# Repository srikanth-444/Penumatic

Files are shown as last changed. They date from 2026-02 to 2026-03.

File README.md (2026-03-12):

# _Peumatic Backpack_
This is a Penumatic System that senses and actuates the multiple soft actuators while communicating with the remote pc 

## _Hardware_ 
To control and sense the robotic actuator system, developed using KiCad 8, this repository will build the Gerber files of the system upon pushing the action artifacts specific to JLCPCB 

| Component | Function | Notes |
| --- | --- | --- |
| **ESP-32 S3** | Microcontroller | Handles system control, communication, and overall logic |
| **LTC2498** | 24-bit ADC | Senses actuator position with high precision |
| **LTC6906** | External oscillator | Provides clock signal for ADC operation |
| **MCZ33996**  | Solenoid driver | Actuates solenoidal valves based on control signals |

## _Firmware_ 
Developed in C using FreeRTOS for increased concurrency. Code is developed using VSCode ESP-IDF extension

### Images
<p align="center">
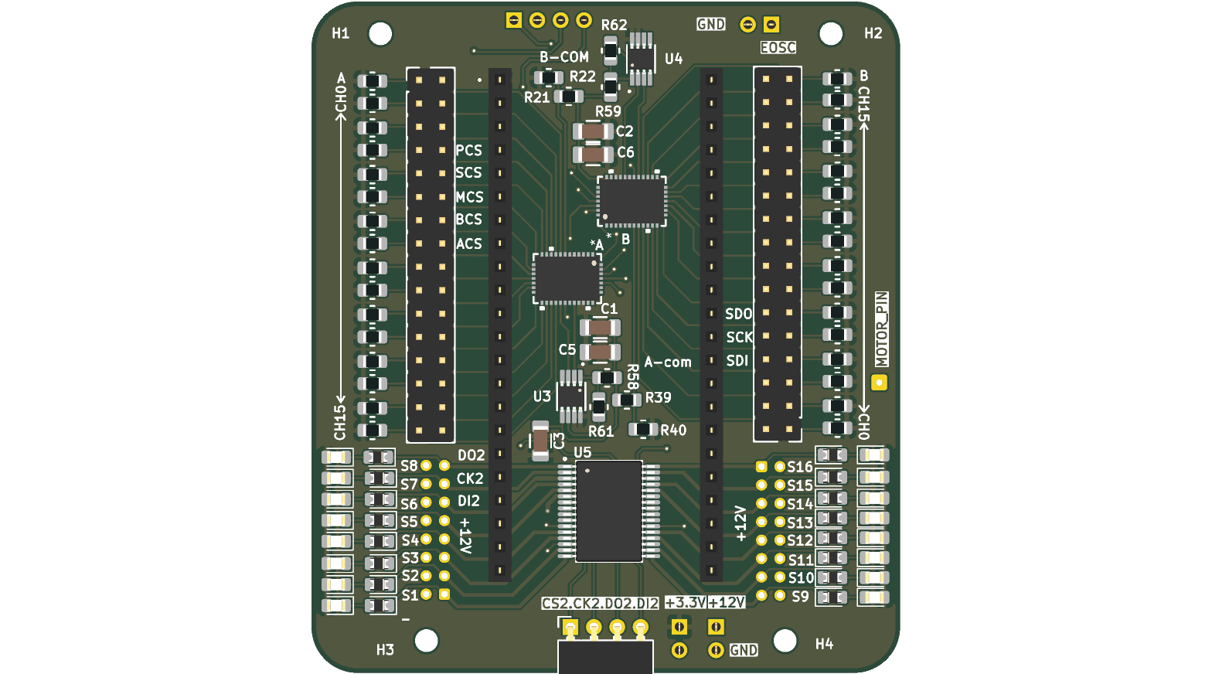
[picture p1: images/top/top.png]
  
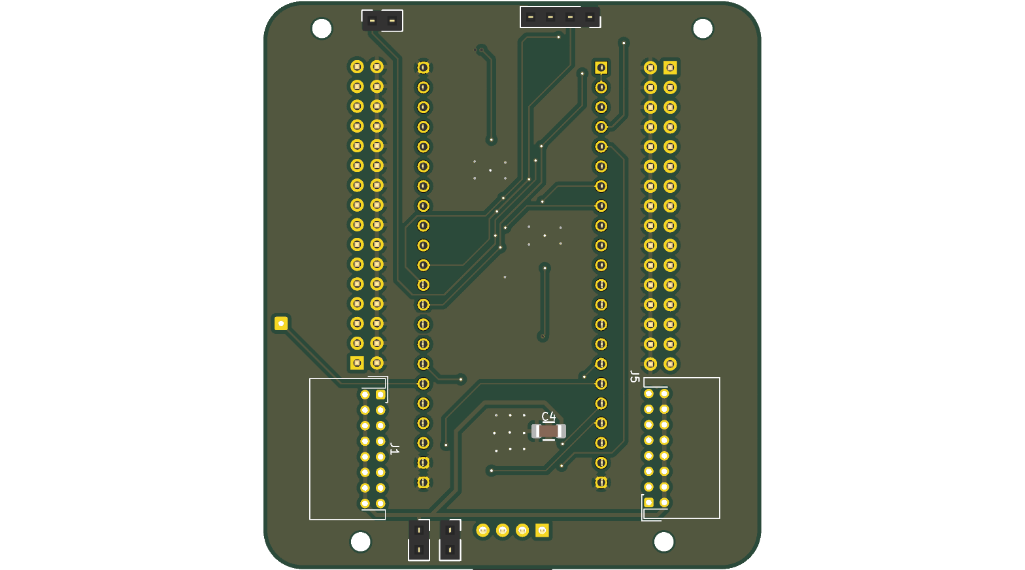
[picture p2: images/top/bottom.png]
  
</p>
<p align="center">
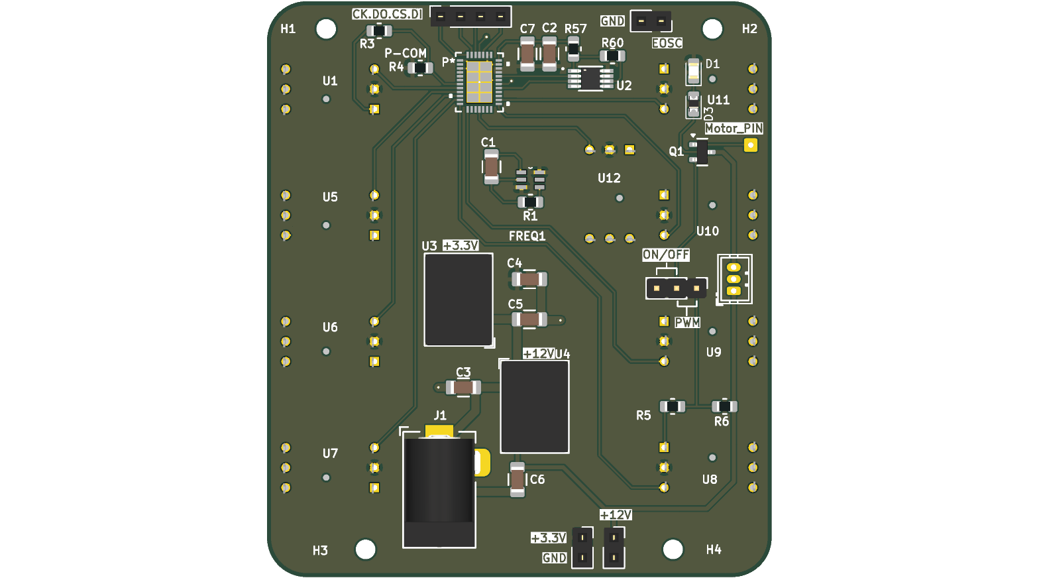
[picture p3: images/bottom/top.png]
  
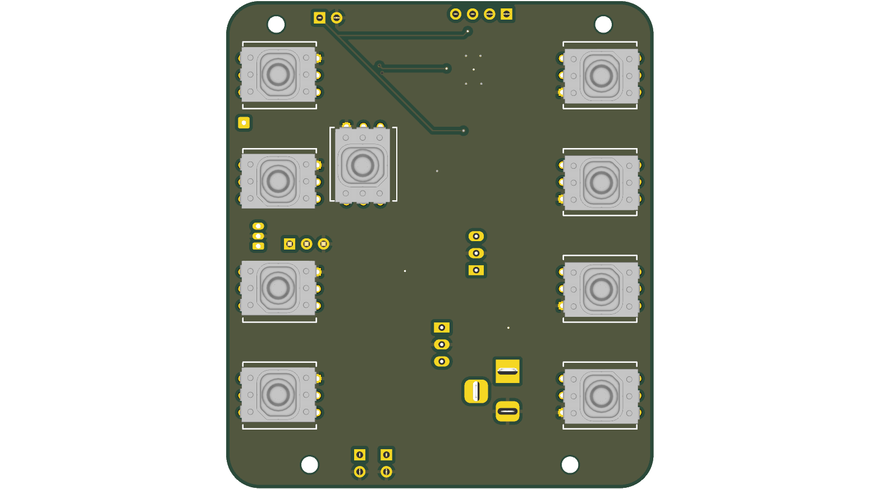
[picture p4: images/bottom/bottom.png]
  
</p>
rendered with [kicad-render](https://github.com/linalinn/kicad-render)

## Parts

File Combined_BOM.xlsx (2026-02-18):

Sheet: pneumatic Backpack v3.0_BOM
Reference | Value | Datasheet | Footprint | Qty | DNP
A1 | LTC2498IUHF_TRPBF |  | mod:QFN-38_UHF | 1
Bus_D1 | Conn_01x04_Pin | ~ | Connector_PinSocket_2.54mm:PinSocket_1x04_P2.54mm_Vertical | 1
C1 | 5pf | ~ | Capacitor_SMD:C_1206_3216Metric_Pad1.33x1.80mm_HandSolder | 1
C2 | 0.1uf | ~ | Capacitor_SMD:C_1206_3216Metric_Pad1.33x1.80mm_HandSolder | 1
C3,C4,C5,C6 | 4.7uf | ~ | Capacitor_SMD:C_1206_3216Metric_Pad1.33x1.80mm_HandSolder | 4
C7 | 10uf | ~ | Capacitor_SMD:C_1206_3216Metric_Pad1.33x1.80mm_HandSolder | 1
D1 | LED | ~ | LED_SMD:LED_0805_2012Metric_Pad1.15x1.40mm_HandSolder | 1
D3 | D | ~ | Diode_SMD:D_0805_2012Metric_Pad1.15x1.40mm_HandSolder | 1
FREQ1 | LTC6906IS6_TRPBF |  | mod:SOT95P280X100-6N | 1
J1 | Barrel_Jack_MountingPin | ~ | Connector_BarrelJack:BarrelJack_Horizontal | 1
J2,J9,J11 | Conn_01x02_Pin | ~ | Connector_PinSocket_2.54mm:PinSocket_1x02_P2.54mm_Vertical | 3
J3,J4 | Conn_01x03_Pin | ~ | -- mixed values -- | 2
J5 | Conn_01x01_Pin | ~ | Connector_Wire:SolderWire-0.15sqmm_1x01_D0.5mm_OD1.5mm | 1
Q1 | AO3400A | http://www.aosmd.com/pdfs/datasheet/AO3400A.pdf | Package_TO_SOT_SMD:SOT-23 | 1
R1,R3,R4,R57,R60 | 100k | ~ | Resistor_SMD:R_0805_2012Metric_Pad1.20x1.40mm_HandSolder | 5
R5 | 70 | ~ | Resistor_SMD:R_0805_2012Metric_Pad1.20x1.40mm_HandSolder | 1
R6 | 50 | ~ | Resistor_SMD:R_0805_2012Metric_Pad1.20x1.40mm_HandSolder | 1
U1,U5,U6,U7,U8,U9,U10,U11,U12 | ABPDLNN100MG2A3 |  | ABPDLNN100MG2A3:XDCR_ABPDLNN100MG2A3 | 9
U2 | INA332AIDGKR |  | INA332AIDGKR:SOP65P490X110-8N | 1
U3 | R-78C3.3-1.0 | https://www.recom-power.com/pdf/Innoline/R-78Cxx-1.0.pdf | Converter_DCDC:Converter_DCDC_RECOM_R-78E-0.5_THT | 1
U4 | R-78C12-1.0 | https://www.recom-power.com/pdf/Innoline/R-78Cxx-1.0.pdf | Converter_DCDC:Converter_DCDC_RECOM_R-78E-0.5_THT | 1

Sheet: pneumatic Backpack v3.1_BOM
Reference | Value | Datasheet | Footprint | Qty | DNP
A2,A3 | LTC2498IUHF_TRPBF |  | mod:QFN-38_UHF | 2
Bus_D1,Bus_D2 | Conn_01x04_Pin | ~ | -- mixed values -- | 2
C1,C2,C3,C4 | 10uf | ~ | Capacitor_SMD:C_1206_3216Metric_Pad1.33x1.80mm_HandSolder | 4
C5,C6 | 0.1uf | ~ | Capacitor_SMD:C_1206_3216Metric_Pad1.33x1.80mm_HandSolder | 2
D1,D2,D3,D4,D5,D6,D7,D8,D9,D10,D11,D12,D13,D14,D15,D16 | LED | ~ | LED_SMD:LED_0805_2012Metric_Pad1.15x1.40mm_HandSolder | 16
J1,J5 | Conn_01x12_Pin | ~ | Connector_JST:JST_ZH_B12B-ZR_1x12_P1.50mm_Vertical | 2
J2 | Conn_01x01_Pin | ~ | Connector_Wire:SolderWire-0.15sqmm_1x01_D0.5mm_OD1.5mm | 1
J3,J4 | Conn_02x16_Top_Bottom | ~ | Connector_PinHeader_2.54mm:PinHeader_2x16_P2.54mm_Vertical | 2
J9,J10,J11 | Conn_01x02_Pin | ~ | Connector_PinSocket_2.54mm:PinSocket_1x02_P2.54mm_Vertical | 3
R21,R22,R23,R24,R25,R26,R27,R28,R29,R30,R31,R32,R33,R34,R35,R36,R37,R38,R39,R40,R41,R42,R43,R44,R45,R46,R47,R48,R49,R50,R51,R52,R53,R54,R55,R56,R58,R59,R61,R62 | 100k | ~ | Resistor_SMD:R_0805_2012Metric_Pad1.20x1.40mm_HandSolder | 40
U1 | ESP32-S3-DEVKITC-1-N8R2 |  | ESP32-S3-DEVKITC-1-N8R2:XCVR_ESP32-S3-DEVKITC-1-N8R2 | 1
U3,U4 | INA332AIDGKR |  | INA332AIDGKR:SOP65P490X110-8N | 2
U5 | MCZ33996EK |  | MCZ33996EK:SOP65P1030X265-33N | 1

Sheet: Summary
Value | Qty
0.1uf | 3
100k | 45
10uf | 5
4.7uf | 4
50 | 1
5pf | 1
70 | 1
ABPDLNN100MG2A3 | 9
AO3400A | 1
Barrel_Jack_MountingPin | 1
Conn_01x01_Pin | 2
Conn_01x02_Pin | 6
Conn_01x03_Pin | 2
Conn_01x04_Pin | 3
Conn_01x12_Pin | 2
Conn_02x16_Top_Bottom | 2
D | 1
ESP32-S3-DEVKITC-1-N8R2 | 1
INA332AIDGKR | 3
LED | 17
LTC2498IUHF_TRPBF | 3
LTC6906IS6_TRPBF | 1
MCZ33996EK | 1
R-78C12-1.0 | 1
R-78C3.3-1.0 | 1

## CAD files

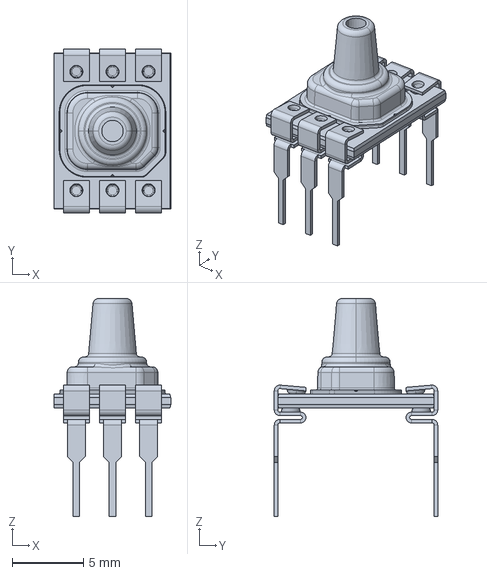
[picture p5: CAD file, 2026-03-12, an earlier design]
Hardware/pneumatic Backpack v3.0/ABPDLNN100MG2A3/ABP2 Series CAD Models/honeywell-abp2-series-32351540_DIP_VN_DRY_a.stp
8.20 x 11.5 x 15.3 mm

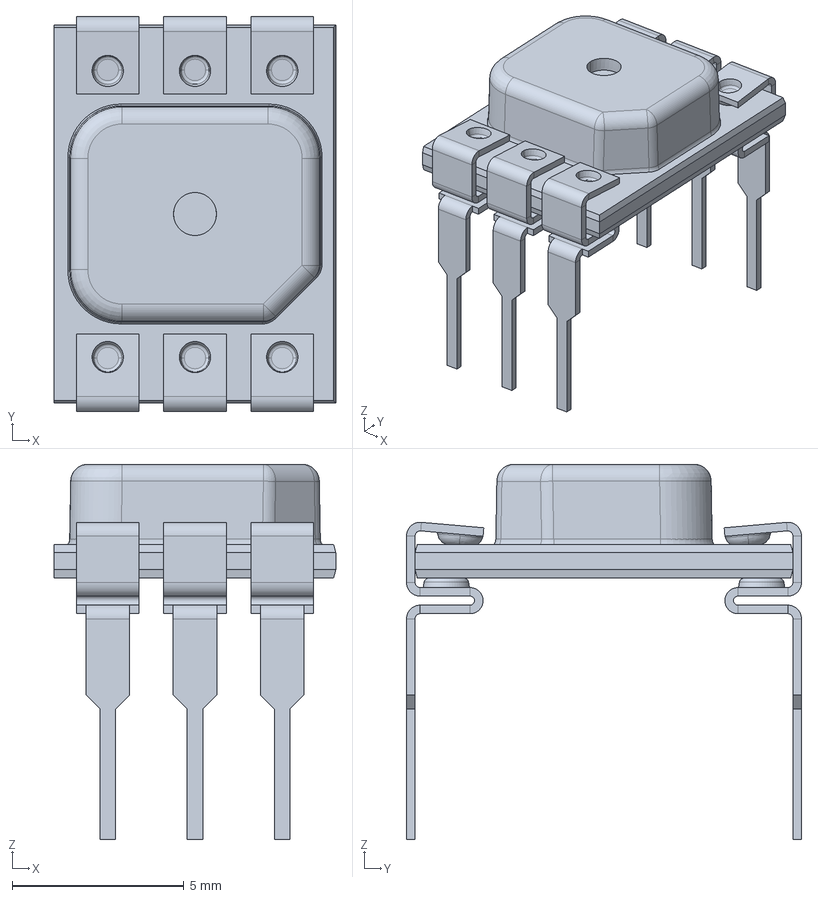
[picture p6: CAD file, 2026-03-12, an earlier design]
Hardware/pneumatic Backpack v3.0/ABPDLNN100MG2A3/honeywell-abp2-series-32351541_DIP_NN_DRY_a.stp
8.20 x 11.5 x 10.9 mm

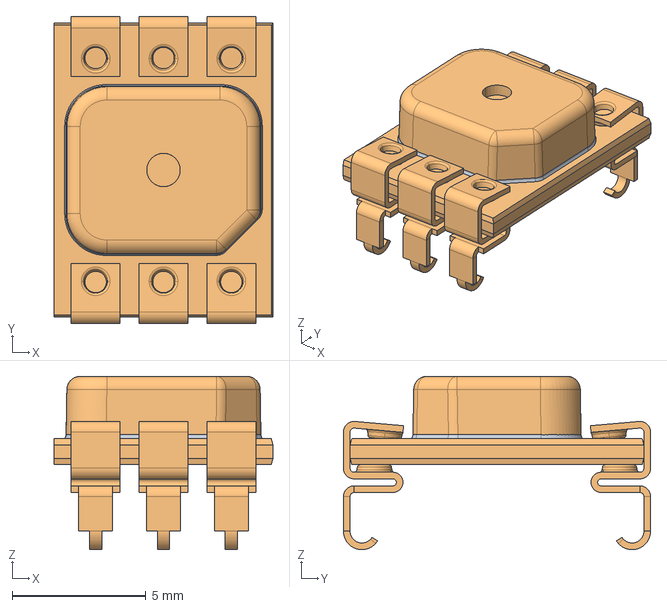
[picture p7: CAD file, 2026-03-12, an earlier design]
Hardware/pneumatic Backpack v3.0/ABPDLNN100MG2A3/ABP2 Series CAD Models/honeywell-abp2-series-32351537_SMT_NN_DRY_a.stp
8.20 x 11.5 x 6.49 mm

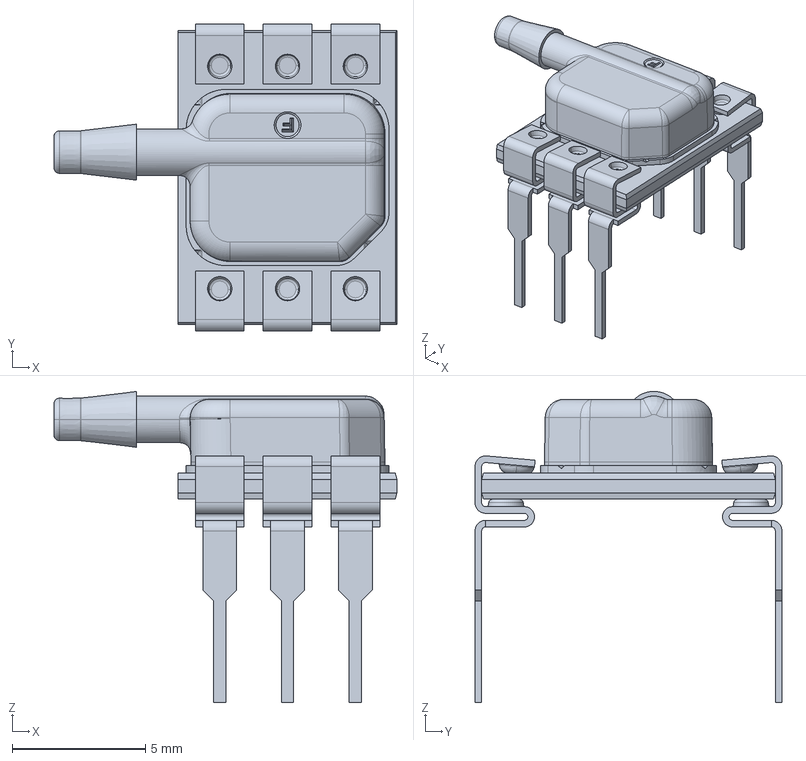
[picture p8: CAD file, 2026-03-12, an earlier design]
Hardware/pneumatic Backpack v3.0/ABPDLNN100MG2A3/honeywell-abp2-series-32351350_DIP_RN_WET_a.stp
12.8 x 11.5 x 11.7 mm

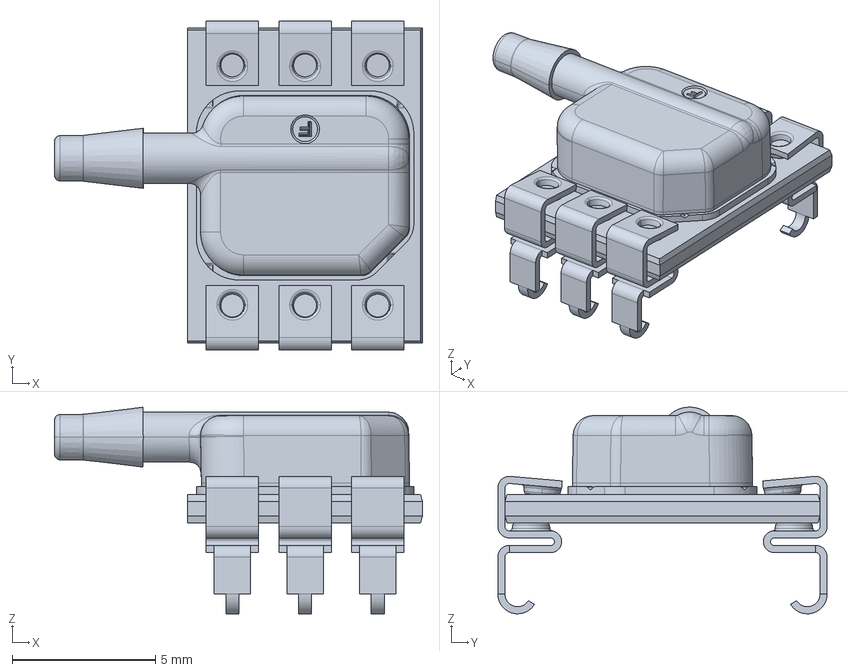
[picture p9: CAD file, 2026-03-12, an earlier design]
Hardware/pneumatic Backpack v3.0/ABPDLNN100MG2A3/ABP2 Series CAD Models/honeywell-abp2-series-32351002_SMT_RN_WET_a.stp
12.8 x 11.5 x 7.22 mm

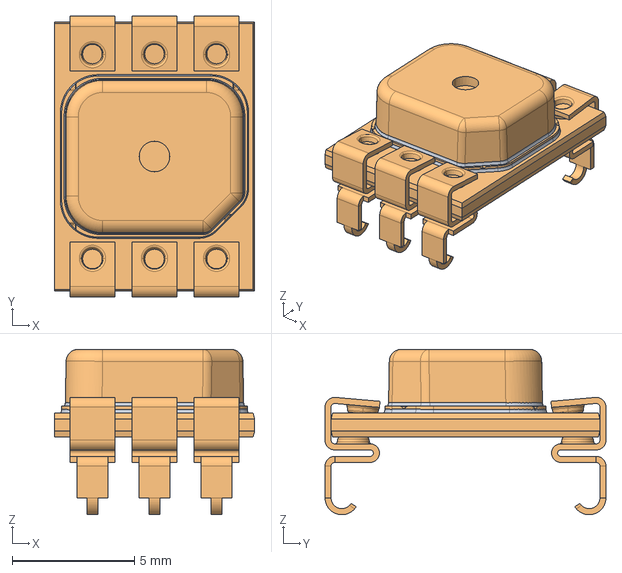
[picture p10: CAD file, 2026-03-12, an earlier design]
Hardware/pneumatic Backpack v3.0/ABPDLNN100MG2A3/ABP2 Series CAD Models/honeywell-abp2-series-32351537_SMT_NN_WET_a.stp
8.20 x 11.5 x 6.77 mm

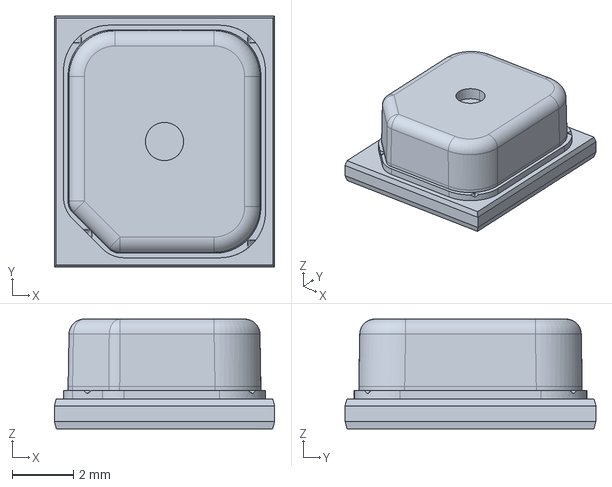
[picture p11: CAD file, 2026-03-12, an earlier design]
Hardware/pneumatic Backpack v3.0/ABPDLNN100MG2A3/ABP2 Series CAD Models/honeywell-abp2-series-32347847_LL_NN_WET_a.stp
7.20 x 8.20 x 3.59 mm

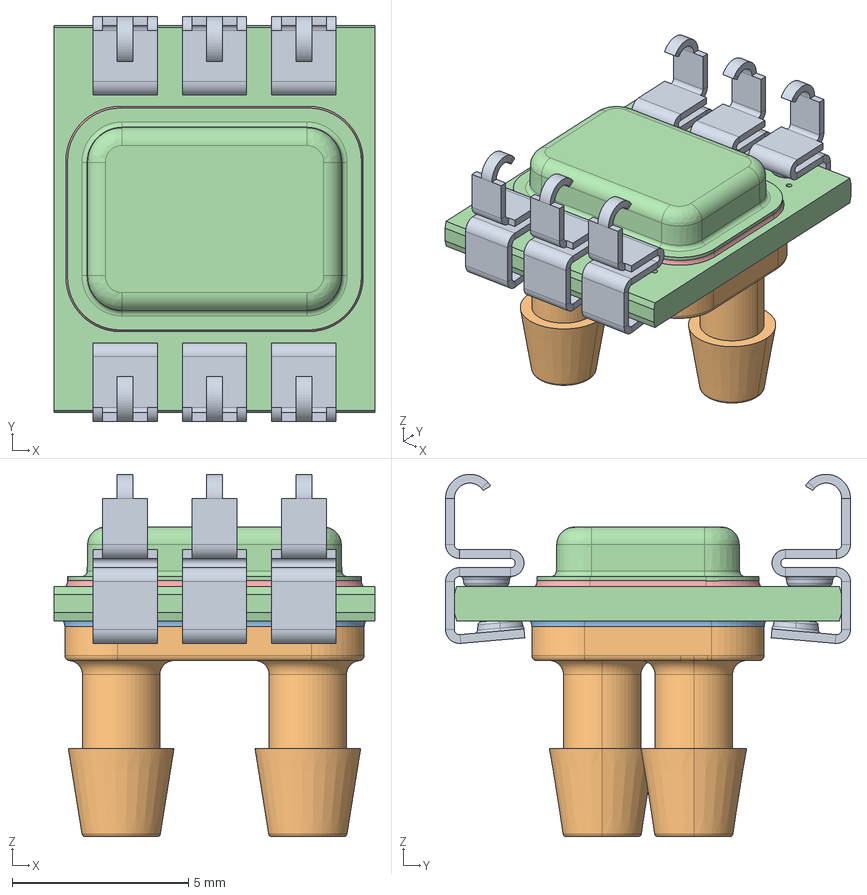
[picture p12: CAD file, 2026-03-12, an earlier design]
Hardware/pneumatic Backpack v3.0/ABPDLNN100MG2A3/ABP2 Series CAD Models/honeywell-abp2-series-32349646_SMT_DA_DRY_a.stp
9.10 x 11.5 x 10.3 mm
MSBR-40_1
MSBR-39_1
MSBR-38_1
MSBR-37_1
MSBR-36_1
MSBR-35_1
MSBR-34_1
MSBR-33_1
MSBR-32_1
MSBR-31_1
MSBR-30_1
MSBR-29_1
MSBR-28_1
MSBR-27_1
MSBR-26_1
MSBR-25_1
MSBR-24_1
MSBR-23_1
MSBR-22_1
MSBR-21_1
MSBR-20_1
MSBR-19_1
MSBR-18_1
MSBR-17_1
MSBR-16_1
MSBR-15_1
MSBR-14_1
MSBR-13_1
MSBR-12_1
MSBR-11_1
MSBR-10_1
MSBR-9_1
MSBR-8_1
MSBR-7_1
MSBR-6_1
MSBR-5_1
MSBR-4_1
MSBR-3_1
MSBR-2_1
MSBR-1_1

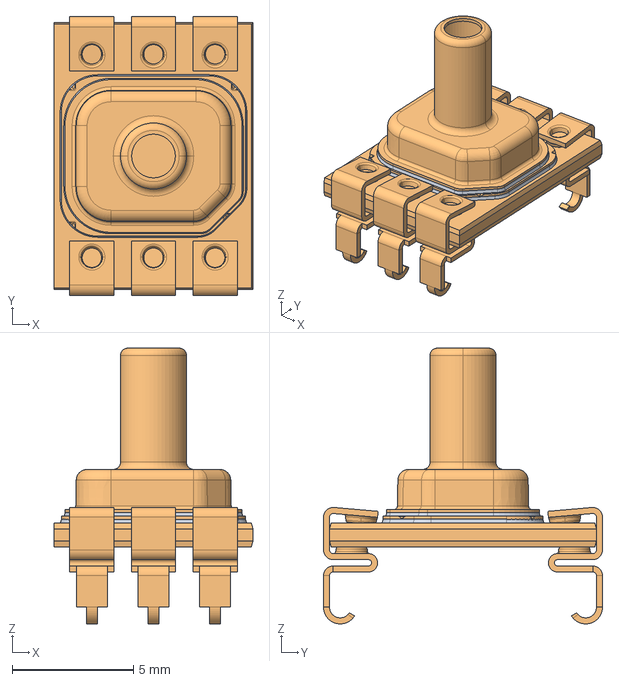
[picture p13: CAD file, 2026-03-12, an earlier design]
Hardware/pneumatic Backpack v3.0/ABPDLNN100MG2A3/ABP2 Series CAD Models/honeywell-abp2-series-32351534_SMT_SN_WET_a.stp
8.20 x 11.5 x 11.4 mm

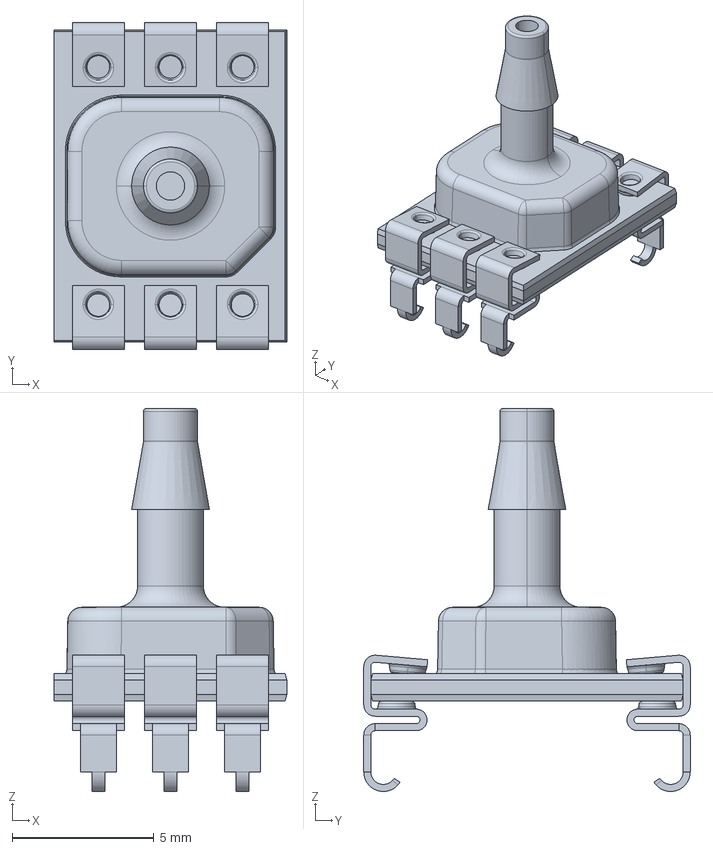
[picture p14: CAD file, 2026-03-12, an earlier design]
Hardware/pneumatic Backpack v3.0/ABPDLNN100MG2A3/ABP2 Series CAD Models/honeywell-abp2-series-32351535_SMT_AN_DRY_a.stp
8.20 x 11.5 x 13.5 mm

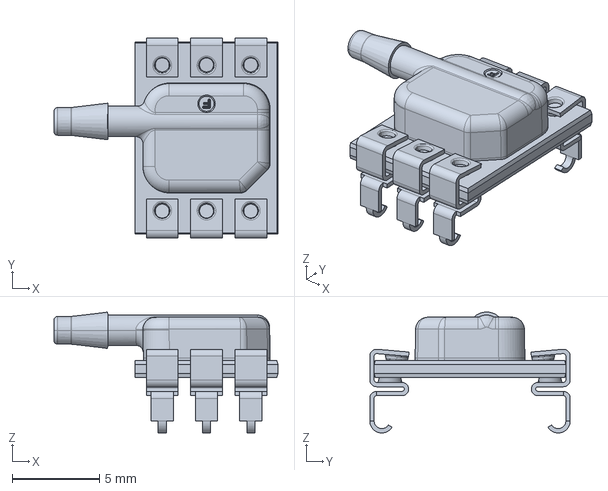
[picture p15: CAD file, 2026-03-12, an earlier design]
Hardware/pneumatic Backpack v3.0/ABPDLNN100MG2A3/ABP2 Series CAD Models/honeywell-abp2-series-32351002_SMT_RN_DRY_a.stp
12.8 x 11.5 x 6.94 mm

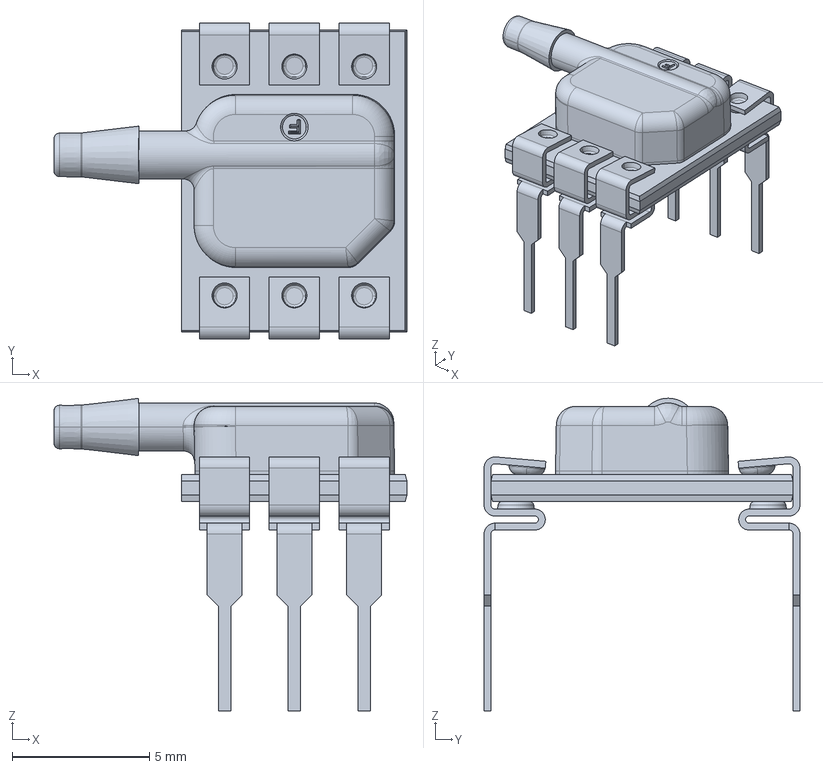
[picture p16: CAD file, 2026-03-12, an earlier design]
Hardware/pneumatic Backpack v3.0/ABPDLNN100MG2A3/ABP2 Series CAD Models/honeywell-abp2-series-32351350_DIP_RN_DRY_a.stp
12.8 x 11.5 x 11.4 mm

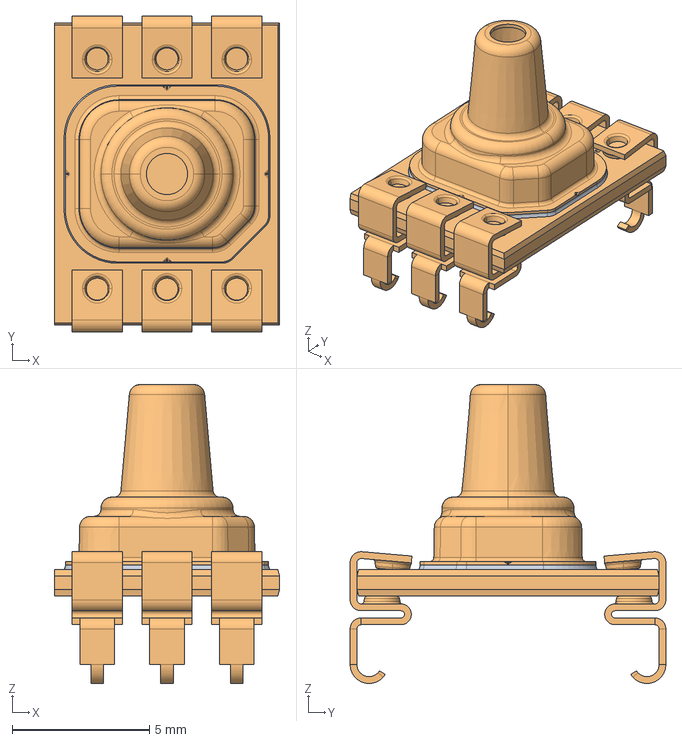
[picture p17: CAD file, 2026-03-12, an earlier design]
Hardware/pneumatic Backpack v3.0/ABPDLNN100MG2A3/ABP2 Series CAD Models/honeywell-abp2-series-32351536_SMT_VN_DRY_a.stp
8.20 x 11.5 x 10.9 mm

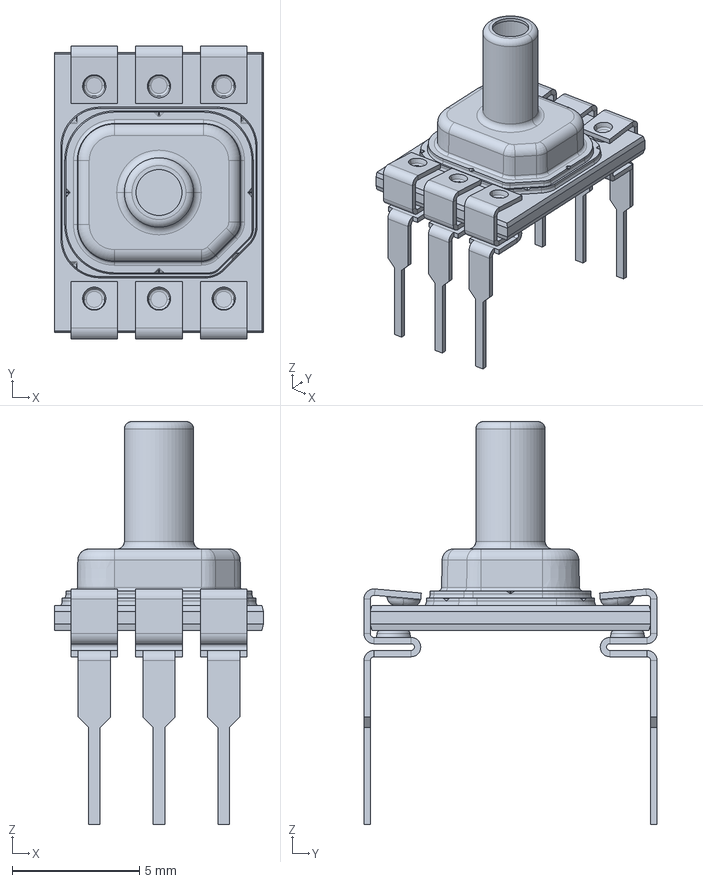
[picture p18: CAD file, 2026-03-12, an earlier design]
Hardware/pneumatic Backpack v3.0/ABPDLNN100MG2A3/ABP2 Series CAD Models/honeywell-abp2-series-32351538_DIP_SN_WET_a.stp
8.20 x 11.5 x 15.8 mm

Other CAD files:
Hardware/pneumatic Backpack v3.0/ABPDLNN100MG2A3/ABP2 Series CAD Models/honeywell-abp2-series-32351536_SMT_VN_WET_a.stp
Hardware/pneumatic Backpack v3.0/ABPDLNN100MG2A3/ABP2 Series CAD Models/honeywell-abp2-series-32349647_DIP_DA_DRY_a.stp
Hardware/pneumatic Backpack v3.0/ABPDLNN100MG2A3/ABP2 Series CAD Models/honeywell-abp2-series-32351535_SMT_AN_WET_a.stp
Hardware/pneumatic Backpack v3.0/ABPDLNN100MG2A3/ABP2 Series CAD Models/honeywell-abp2-series-32351309_DIP_RR_DRY_a.stp
Hardware/pneumatic Backpack v3.0/ABPDLNN100MG2A3/ABP2 Series CAD Models/honeywell-abp2-series-32347845_LL_AN_WET_a.stp
Hardware/pneumatic Backpack v3.0/ABPDLNN100MG2A3/ABP2 Series CAD Models/honeywell-abp2-series-32347846_LL_SN_WET_a.stp
Hardware/pneumatic Backpack v3.0/ABPDLNN100MG2A3/ABP2 Series CAD Models/honeywell-abp2-series-32347847_LL_NN_DRY_a.stp
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

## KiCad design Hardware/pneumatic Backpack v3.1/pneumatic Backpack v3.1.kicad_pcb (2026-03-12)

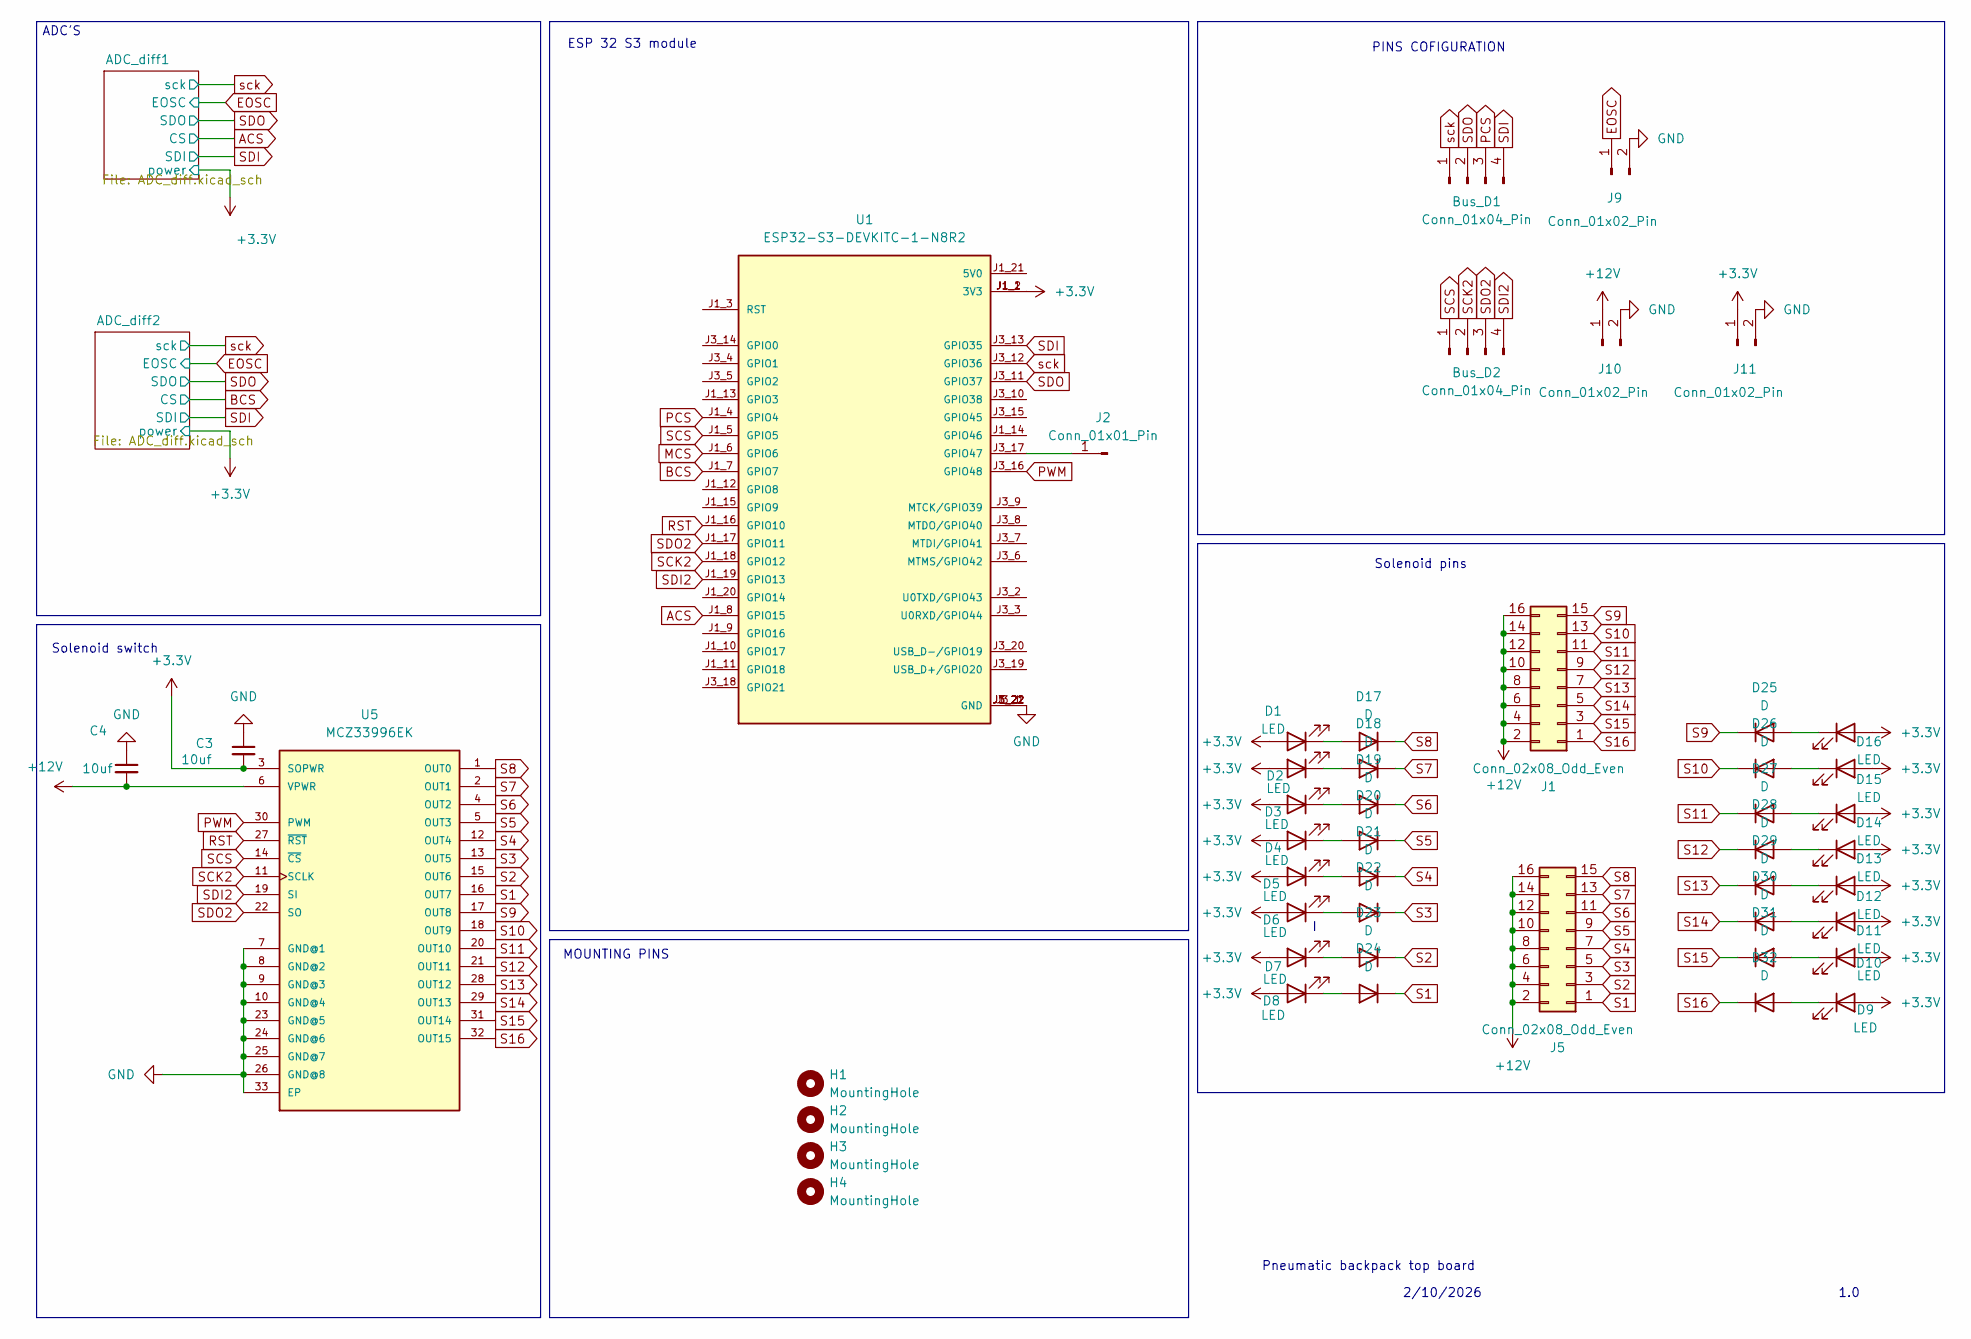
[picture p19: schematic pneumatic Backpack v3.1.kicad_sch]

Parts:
Bus_D1: Conn_01x04_Pin; PinSocket_1x04_P2.54mm_Vertical
Bus_D2: Conn_01x04_Pin; PinSocket_1x04_P2.54mm_Horizontal
C3, C4: 10uf; C_1206_3216Metric_Pad1.33x1.80mm_HandSolder
D1, D2, D3, D4, D5, D6, D7, D8, D9, D10, D11, D12, D13, D14, D15, D16: LED; LED_0805_2012Metric_Pad1.15x1.40mm_HandSolder
D17, D18, D19, D20, D21, D22, D23, D24, D25, D26, D27, D28, D29, D30, D31, D32: D; D_0805_2012Metric_Pad1.15x1.40mm_HandSolder
H1, H2, H3, H4: MountingHole; MountingHole_2.5mm
J1, J5: Conn_02x08_Odd_Even; JST_PHD_S16B-PHDSS_2x08_P2.00mm_Horizontal
J2: Conn_01x01_Pin; SolderWire-0.15sqmm_1x01_D0.5mm_OD1.5mm
J9, J10, J11: Conn_01x02_Pin; PinSocket_1x02_P2.54mm_Vertical
U1: ESP32-S3-DEVKITC-1-N8R2; XCVR_ESP32-S3-DEVKITC-1-N8R2; PARTREV V1
U5: MCZ33996EK; SOP65P1030X265-33N

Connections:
+3.3V: C3.2, D1.2 (A), D2.2 (A), D3.2 (A), D4.2 (A), D5.2 (A), D6.2 (A), D7.2 (A), D8.2 (A), D9.2 (A), D10.2 (A), D11.2 (A), D12.2 (A), D13.2 (A), D14.2 (A), D15.2 (A), D16.2 (A), J11.1, U1.J1_1 (3V3), U1.J1_2 (3V3), U5.3 (SOPWR); also elsewhere on the board
+12V: C4.2, J1.2, J1.4, J1.6, J1.8, J1.10, J1.12, J1.14, J1.16, J5.2, J5.4, J5.6, J5.8, J5.10, J5.12, J5.14, J5.16, J10.1, U5.6 (VPWR)
ACS: U1.J1_8 (GPIO15); also elsewhere on the board
BCS: U1.J1_7 (GPIO7); also elsewhere on the board
EOSC: J9.1; also elsewhere on the board
GND: C3.1, C4.1, J9.2, J10.2, J11.2, U1.J1_22 (GND), U1.J3_1 (GND), U1.J3_21 (GND), U1.J3_22 (GND), U5.7 (GND@1), U5.8 (GND@2), U5.9 (GND@3), U5.10 (GND@4), U5.23 (GND@5), U5.24 (GND@6), U5.25 (GND@7), U5.26 (GND@8), U5.33 (EP); also elsewhere on the board
MCS: U1.J1_6 (GPIO6)
unnamed: D1.1 (K), D17.2 (A)
unnamed: D10.1 (K), D31.2 (A)
unnamed: D11.1 (K), D30.2 (A)
unnamed: D12.1 (K), D29.2 (A)
unnamed: D13.1 (K), D28.2 (A)
unnamed: D14.1 (K), D27.2 (A)
unnamed: D15.1 (K), D26.2 (A)
unnamed: D16.1 (K), D25.2 (A)
unnamed: D2.1 (K), D18.2 (A)
unnamed: D3.1 (K), D19.2 (A)
unnamed: D4.1 (K), D20.2 (A)
unnamed: D5.1 (K), D21.2 (A)
unnamed: D6.1 (K), D22.2 (A)
unnamed: D7.1 (K), D23.2 (A)
unnamed: D8.1 (K), D24.2 (A)
unnamed: D9.1 (K), D32.2 (A)
unnamed: J2.1, U1.J3_17 (GPIO47)
PCS: Bus_D1.3, U1.J1_4 (GPIO4)
PWM: U1.J3_16 (GPIO48), U5.30 (PWM)
RST: U1.J1_16 (GPIO10), U5.27 (~RST)
S1: D24.1 (K), J5.1, U5.16 (OUT7)
S2: D23.1 (K), J5.3, U5.15 (OUT6)
S3: D22.1 (K), J5.5, U5.13 (OUT5)
S4: D21.1 (K), J5.7, U5.12 (OUT4)
S5: D20.1 (K), J5.9, U5.5 (OUT3)
S6: D19.1 (K), J5.11, U5.4 (OUT2)
S7: D18.1 (K), J5.13, U5.2 (OUT1)
S8: D17.1 (K), J5.15, U5.1 (OUT0)
S9: D25.1 (K), J1.15, U5.17 (OUT8)
S10: D26.1 (K), J1.13, U5.18 (OUT9)
S11: D27.1 (K), J1.11, U5.20 (OUT10)
S12: D28.1 (K), J1.9, U5.21 (OUT11)
S13: D29.1 (K), J1.7, U5.28 (OUT12)
S14: D30.1 (K), J1.5, U5.29 (OUT13)
S15: D31.1 (K), J1.3, U5.31 (OUT14)
S16: D32.1 (K), J1.1, U5.32 (OUT15)
SCK2: Bus_D2.2, U1.J1_18 (GPIO12), U5.11 (SCLK)
SCS: Bus_D2.1, U1.J1_5 (GPIO5), U5.14 (~CS)
SDI: Bus_D1.4, U1.J3_13 (GPIO35); also elsewhere on the board
SDI2: Bus_D2.4, U1.J1_19 (GPIO13), U5.19 (SI)
SDO: Bus_D1.2, U1.J3_11 (GPIO37); also elsewhere on the board
SDO2: Bus_D2.3, U1.J1_17 (GPIO11), U5.22 (SO)
sck: Bus_D1.1, U1.J3_12 (GPIO36); also elsewhere on the board

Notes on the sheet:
ADC'S
Solenoid pins
Solenoid switch
MOUNTING PINS
ESP 32 S3 module
Pneumatic backpack top board
1.0
2/10/2026
PINS COFIGURATION

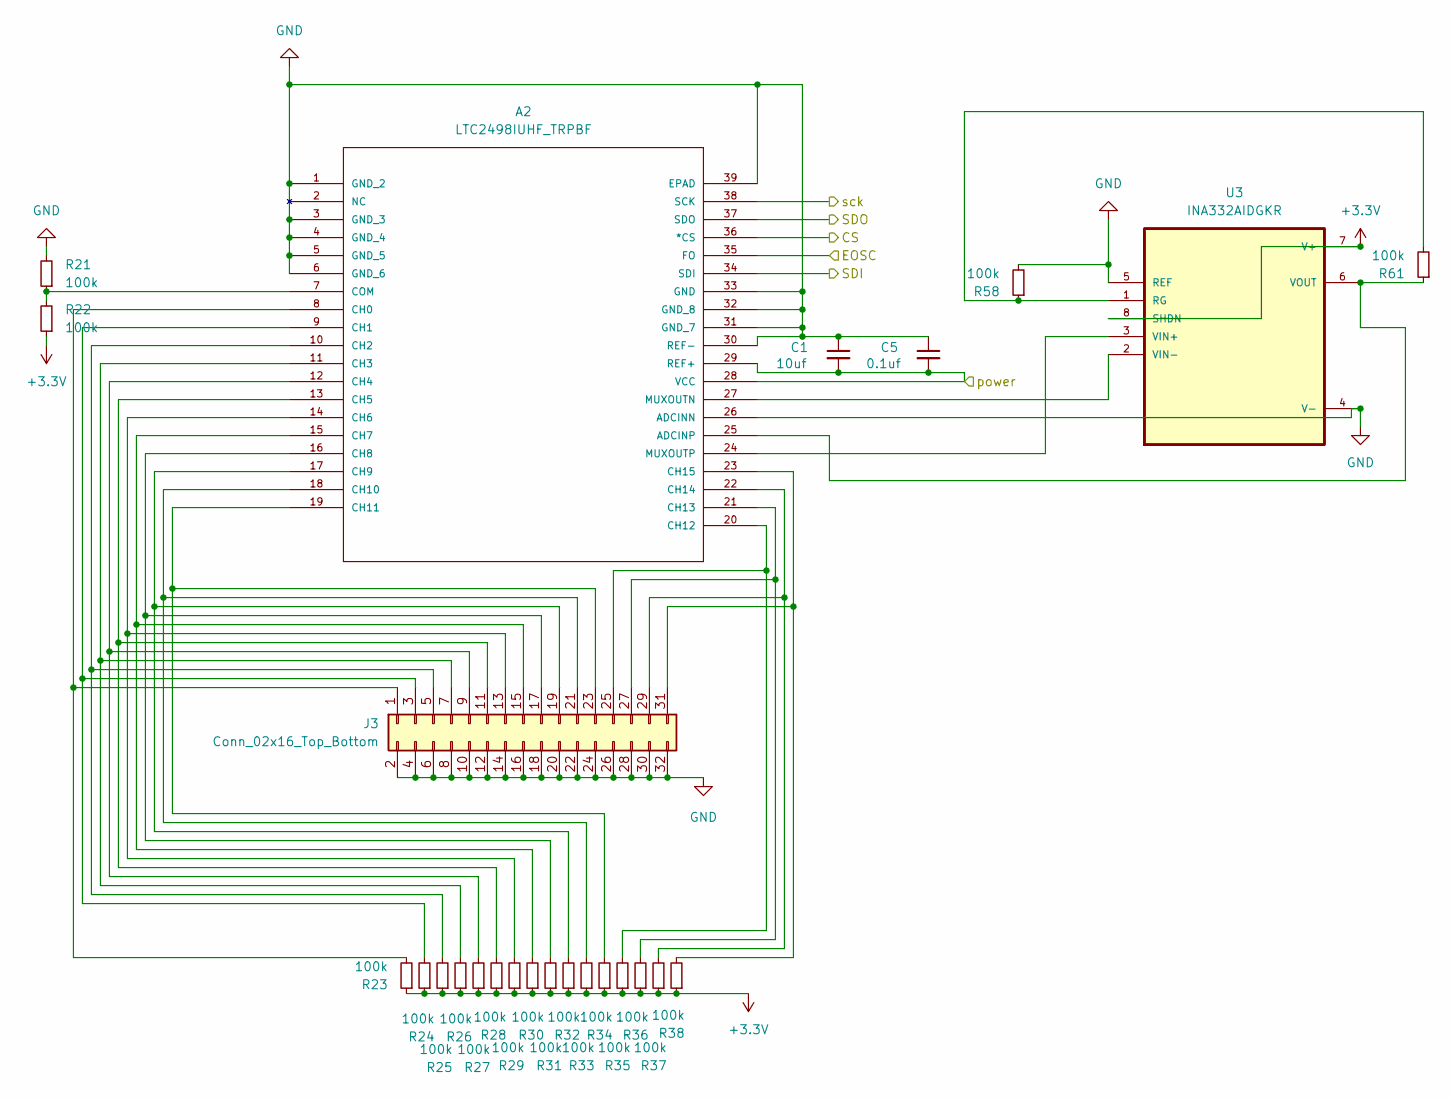
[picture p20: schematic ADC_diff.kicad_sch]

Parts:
A2: LTC2498IUHF_TRPBF; QFN-38_UHF; MANUFACTURER_PART_NUMBER ltc2498iuhf
C1: 10uf; C_1206_3216Metric_Pad1.33x1.80mm_HandSolder
C5: 0.1uf; C_1206_3216Metric_Pad1.33x1.80mm_HandSolder
J3: Conn_02x16_Top_Bottom; PinHeader_2x16_P2.54mm_Vertical
R21, R22, R23, R24, R25, R26, R27, R28, R29, R30, R31, R32, R33, R34, R35, R36, R37, R38, R58, R61: 100k; R_0805_2012Metric_Pad1.20x1.40mm_HandSolder
U3: INA332AIDGKR; SOP65P490X110-8N

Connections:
+3.3V: A2.28 (VCC), A2.29 (REF+), C1.2, C5.2, R22.1, R23.1, R24.1, R25.1, R26.1, R27.1, R28.1, R29.1, R30.1, R31.1, R32.1, R33.1, R34.1, R35.1, R36.1, R37.1, R38.1, U3.7 (V+), U3.8 (SHDN); also elsewhere on the board
ACS: A2.36 (*CS); also elsewhere on the board
EOSC: A2.35 (FO); also elsewhere on the board
GND: A2.1 (GND_2), A2.3 (GND_3), A2.4 (GND_4), A2.5 (GND_5), A2.6 (GND_6), A2.26 (ADCINN), A2.30 (REF-), A2.31 (GND_7), A2.32 (GND_8), A2.33 (GND), A2.39 (EPAD), C1.1, C5.1, J3.2, J3.4, J3.6, J3.8, J3.10, J3.12, J3.14, J3.16, J3.18, J3.20, J3.22, J3.24, J3.26, J3.28, J3.30, J3.32, R21.2, R58.2, U3.4 (V-), U3.5 (REF); also elsewhere on the board
unnamed: A2.25 (ADCINP), R61.1, U3.6 (VOUT)
unnamed: A2.8 (CH0), J3.1, R23.2
unnamed: A2.9 (CH1), J3.3, R24.2
unnamed: A2.10 (CH2), J3.5, R25.2
unnamed: A2.11 (CH3), J3.7, R26.2
unnamed: A2.12 (CH4), J3.9, R27.2
unnamed: A2.13 (CH5), J3.11, R28.2
unnamed: A2.14 (CH6), J3.13, R29.2
unnamed: A2.15 (CH7), J3.15, R30.2
unnamed: A2.16 (CH8), J3.17, R31.2
unnamed: A2.17 (CH9), J3.19, R32.2
unnamed: A2.18 (CH10), J3.21, R33.2
unnamed: A2.19 (CH11), J3.23, R34.2
unnamed: A2.20 (CH12), J3.25, R35.2
unnamed: A2.21 (CH13), J3.27, R36.2
unnamed: A2.22 (CH14), J3.29, R37.2
unnamed: A2.23 (CH15), J3.31, R38.2
unnamed: A2.7 (COM), R21.1, R22.2
unnamed: A2.27 (MUXOUTN), U3.2 (VIN-)
unnamed: A2.24 (MUXOUTP), U3.3 (VIN+)
unnamed: R58.1, R61.2, U3.1 (RG)
SDI: A2.34 (SDI); also elsewhere on the board
SDO: A2.37 (SDO); also elsewhere on the board
sck: A2.38 (SCK); also elsewhere on the board

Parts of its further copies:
A3: LTC2498IUHF_TRPBF; QFN-38_UHF; MANUFACTURER_PART_NUMBER ltc2498iuhf
C2: 10uf; C_1206_3216Metric_Pad1.33x1.80mm_HandSolder
C6: 0.1uf; C_1206_3216Metric_Pad1.33x1.80mm_HandSolder
J4: Conn_02x16_Top_Bottom; PinHeader_2x16_P2.54mm_Vertical
R39, R40, R41, R42, R43, R44, R45, R46, R47, R48, R49, R50, R51, R52, R53, R54, R55, R56, R59, R62: 100k; R_0805_2012Metric_Pad1.20x1.40mm_HandSolder
U4: INA332AIDGKR; SOP65P490X110-8N

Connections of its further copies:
+3.3V: A3.28 (VCC), A3.29 (REF+), C2.2, C6.2, R40.1, R41.1, R42.1, R43.1, R44.1, R45.1, R46.1, R47.1, R48.1, R49.1, R50.1, R51.1, R52.1, R53.1, R54.1, R55.1, R56.1, U4.7 (V+), U4.8 (SHDN); also elsewhere on the board
BCS: A3.36 (*CS); also elsewhere on the board
EOSC: A3.35 (FO); also elsewhere on the board
GND: A3.1 (GND_2), A3.3 (GND_3), A3.4 (GND_4), A3.5 (GND_5), A3.6 (GND_6), A3.26 (ADCINN), A3.30 (REF-), A3.31 (GND_7), A3.32 (GND_8), A3.33 (GND), A3.39 (EPAD), C2.1, C6.1, J4.2, J4.4, J4.6, J4.8, J4.10, J4.12, J4.14, J4.16, J4.18, J4.20, J4.22, J4.24, J4.26, J4.28, J4.30, J4.32, R39.2, R59.2, U4.4 (V-), U4.5 (REF); also elsewhere on the board
unnamed: A3.25 (ADCINP), R62.1, U4.6 (VOUT)
unnamed: A3.8 (CH0), J4.1, R41.2
unnamed: A3.9 (CH1), J4.3, R42.2
unnamed: A3.10 (CH2), J4.5, R43.2
unnamed: A3.11 (CH3), J4.7, R44.2
unnamed: A3.12 (CH4), J4.9, R45.2
unnamed: A3.13 (CH5), J4.11, R46.2
unnamed: A3.14 (CH6), J4.13, R47.2
unnamed: A3.15 (CH7), J4.15, R48.2
unnamed: A3.16 (CH8), J4.17, R49.2
unnamed: A3.17 (CH9), J4.19, R50.2
unnamed: A3.18 (CH10), J4.21, R51.2
unnamed: A3.19 (CH11), J4.23, R52.2
unnamed: A3.20 (CH12), J4.25, R53.2
unnamed: A3.21 (CH13), J4.27, R54.2
unnamed: A3.22 (CH14), J4.29, R55.2
unnamed: A3.23 (CH15), J4.31, R56.2
unnamed: A3.7 (COM), R39.1, R40.2
unnamed: A3.27 (MUXOUTN), U4.2 (VIN-)
unnamed: A3.24 (MUXOUTP), U4.3 (VIN+)
unnamed: R59.1, R62.2, U4.1 (RG)
SDI: A3.34 (SDI); also elsewhere on the board
SDO: A3.37 (SDO); also elsewhere on the board
sck: A3.38 (SCK); also elsewhere on the board

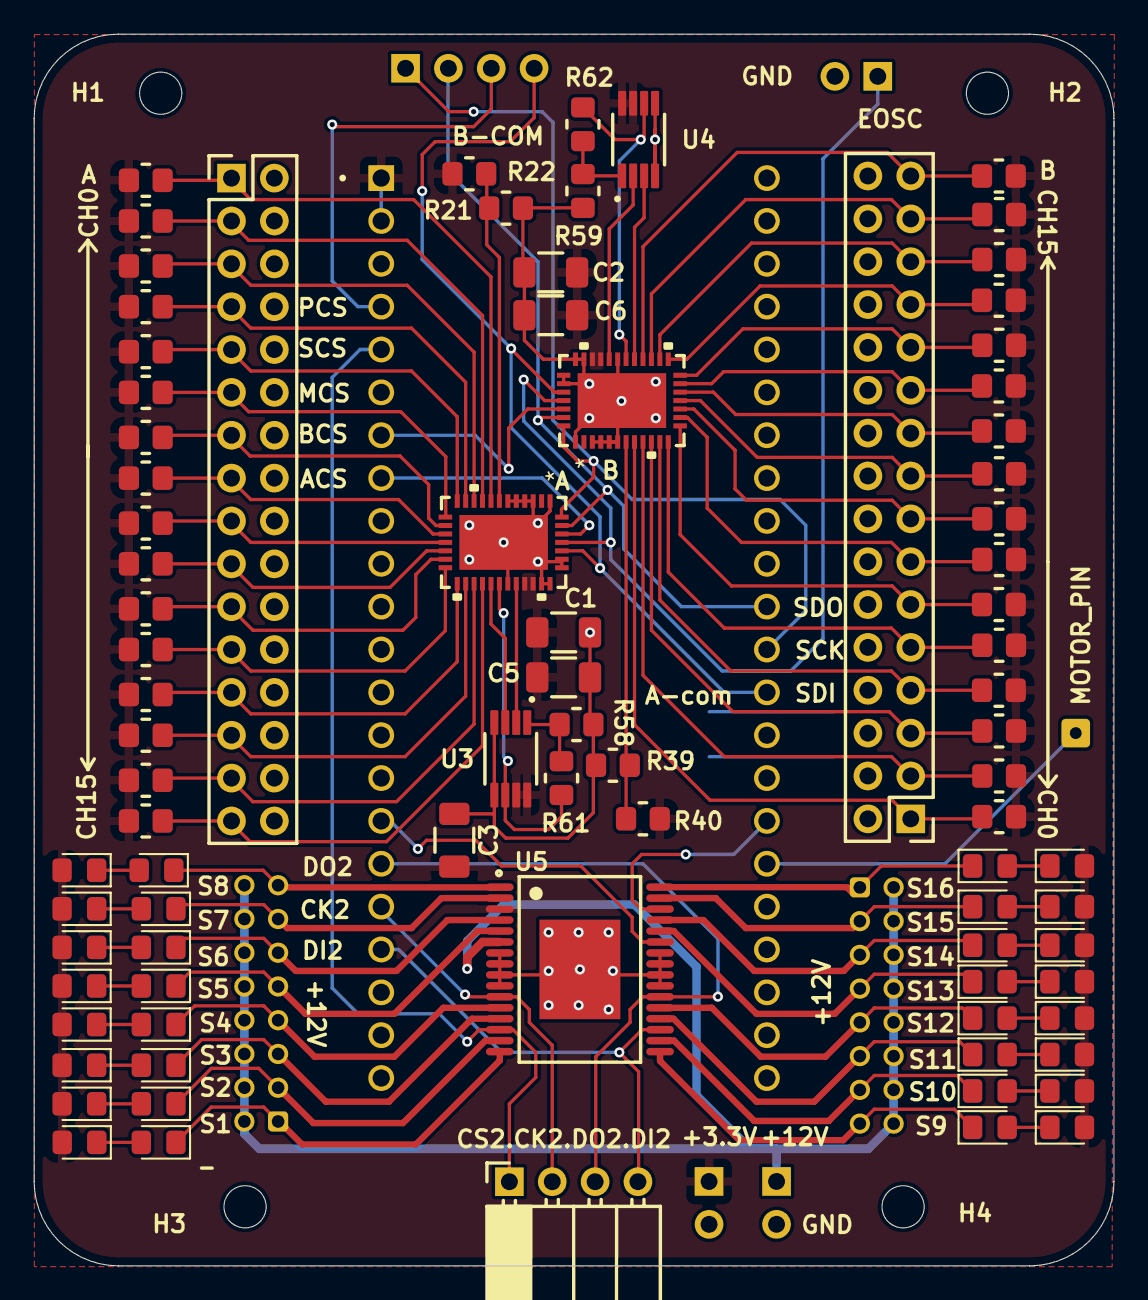
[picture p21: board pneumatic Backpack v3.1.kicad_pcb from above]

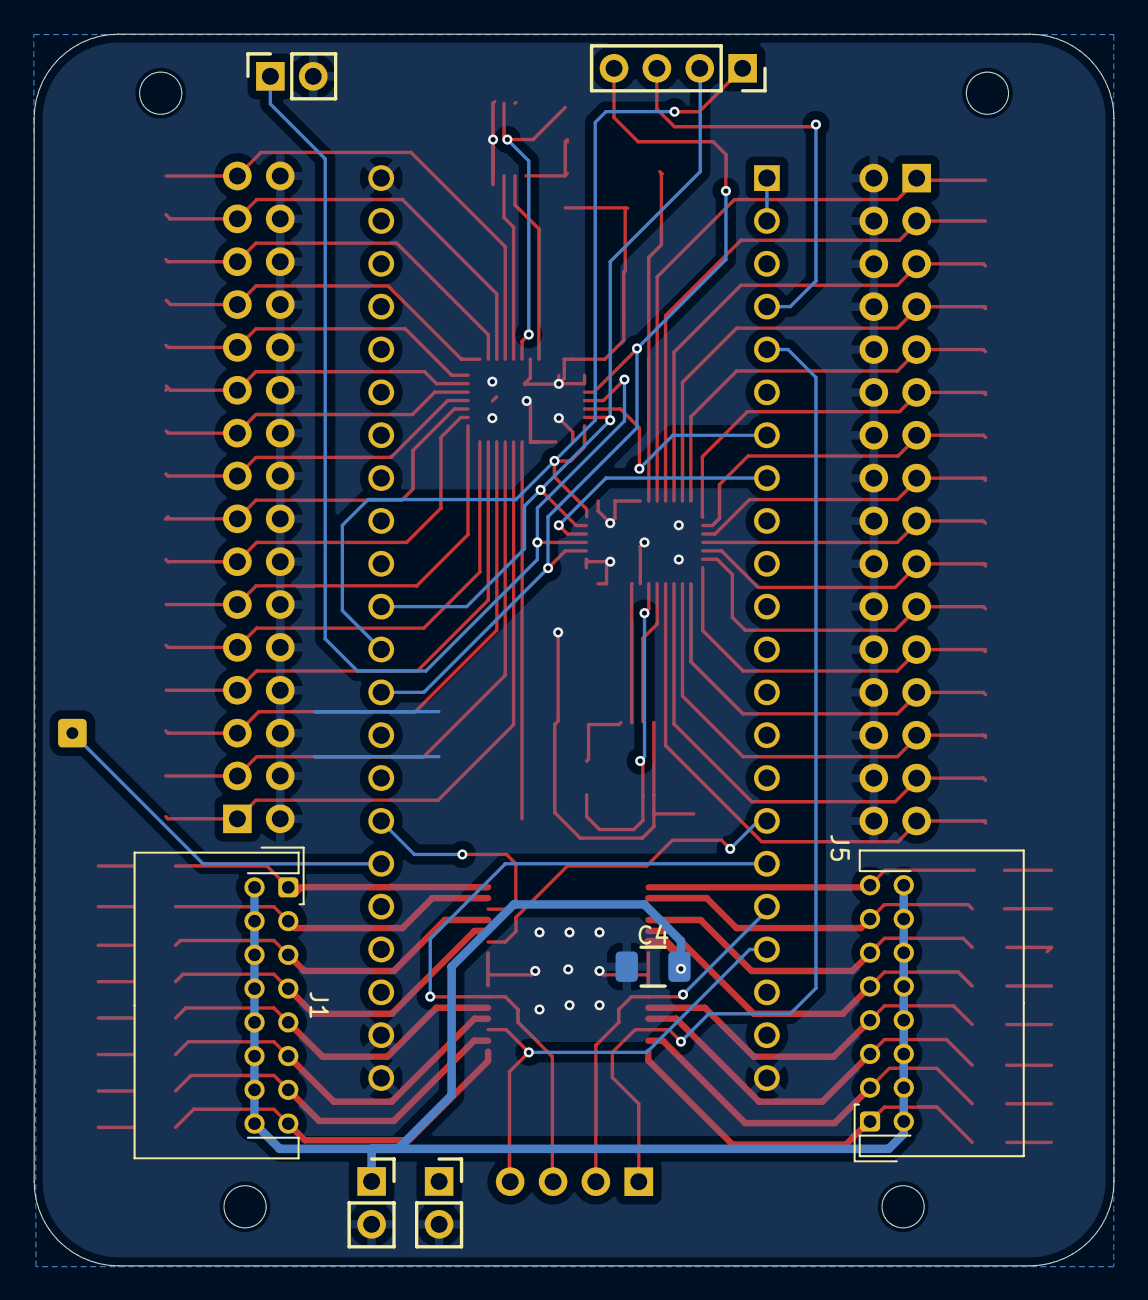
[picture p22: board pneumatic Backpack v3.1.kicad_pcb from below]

Board: 2 copper layers, 64.0 x 73.0 mm, 98 parts (7 on the bottom side), 91 nets.

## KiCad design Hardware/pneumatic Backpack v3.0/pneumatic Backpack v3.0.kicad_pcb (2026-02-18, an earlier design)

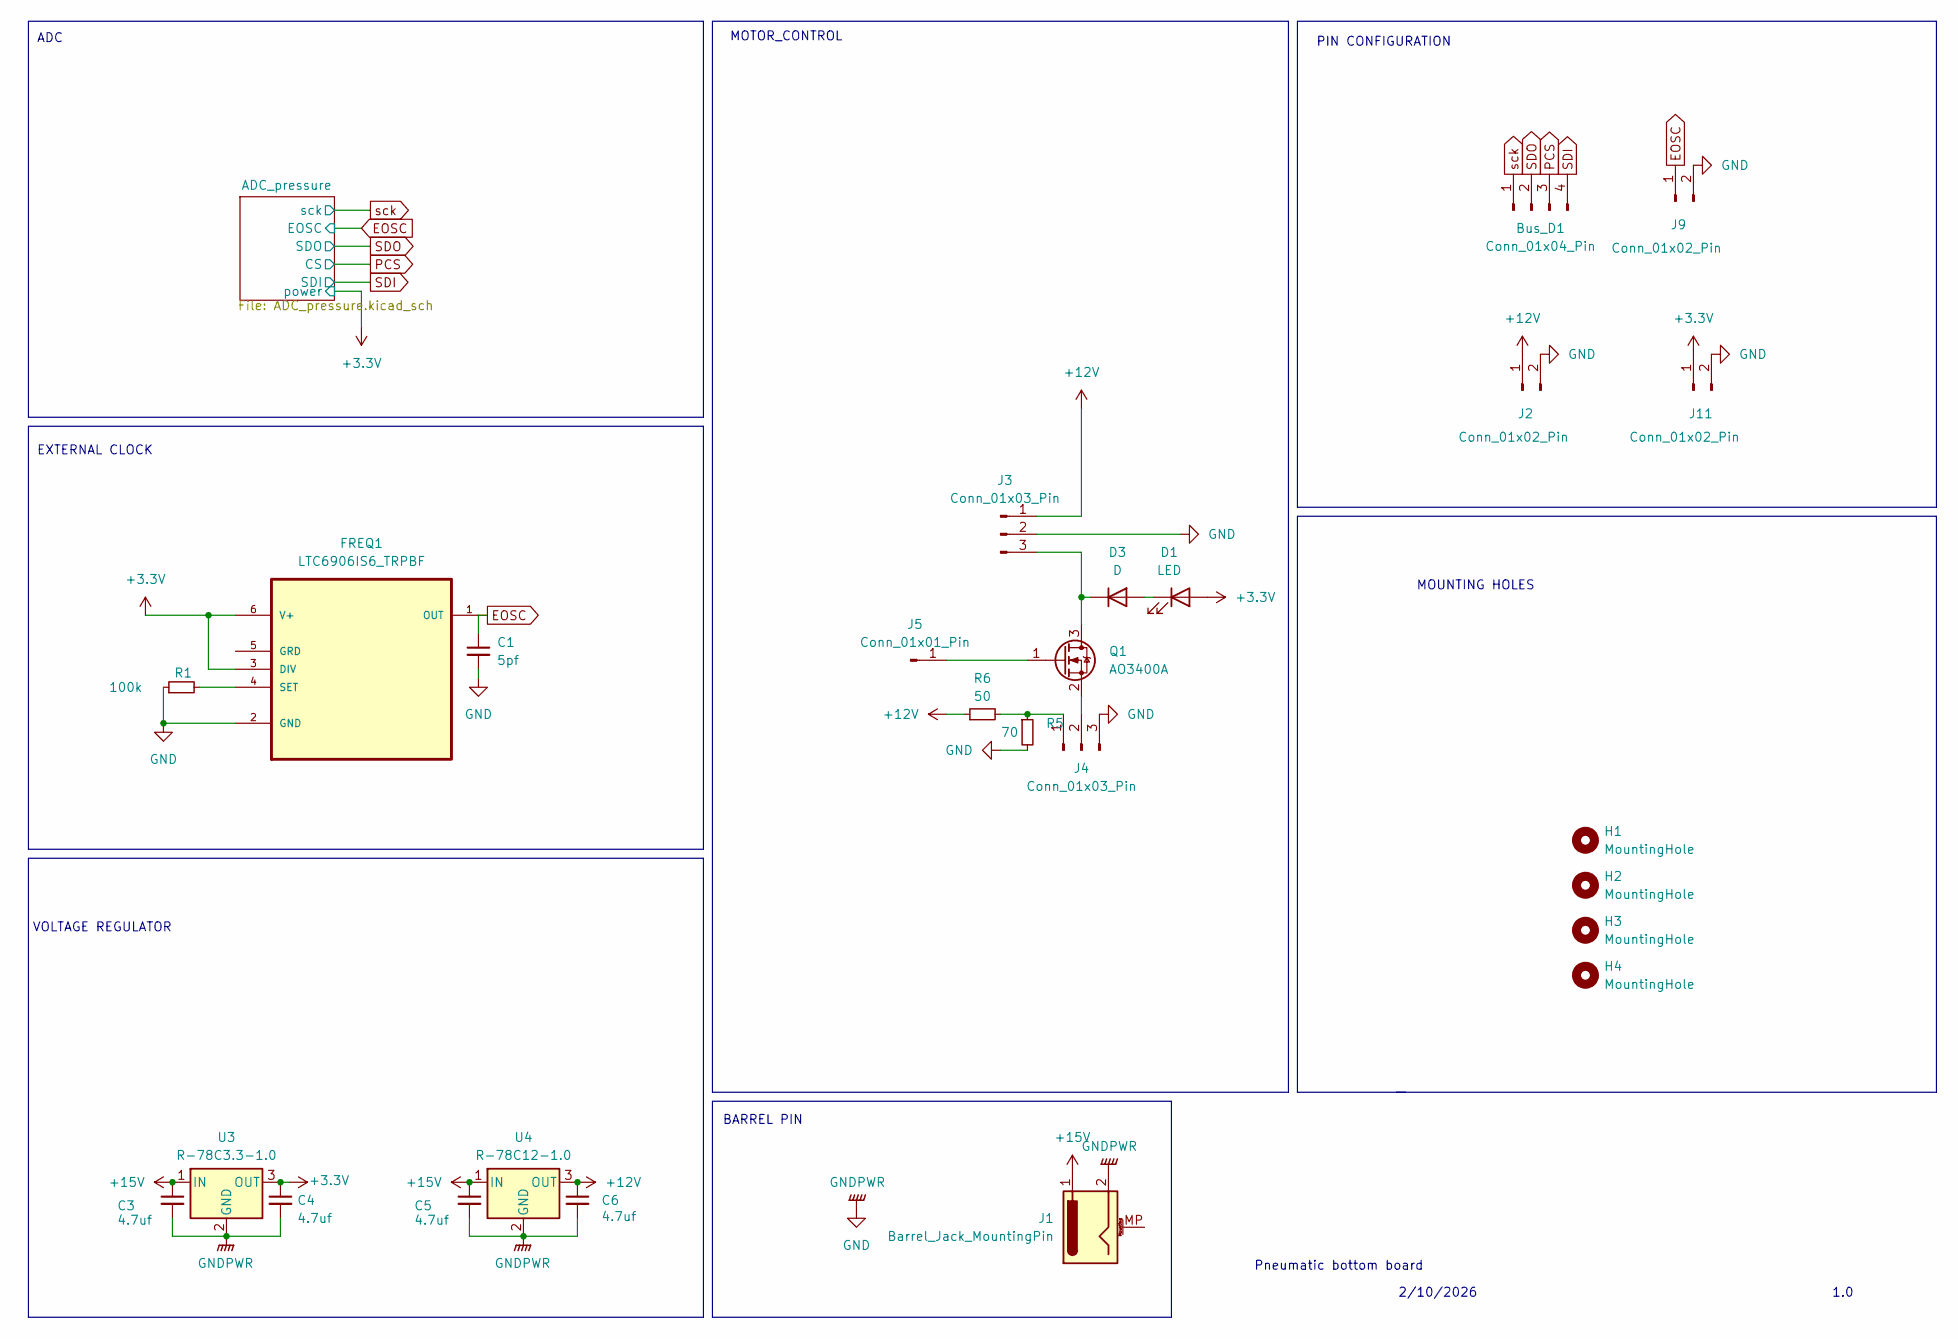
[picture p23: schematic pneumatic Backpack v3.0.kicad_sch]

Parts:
Bus_D1: Conn_01x04_Pin; PinSocket_1x04_P2.54mm_Vertical
C1: 5pf; C_1206_3216Metric_Pad1.33x1.80mm_HandSolder
C3, C4, C5, C6: 4.7uf; C_1206_3216Metric_Pad1.33x1.80mm_HandSolder
D1: LED; LED_0805_2012Metric_Pad1.15x1.40mm_HandSolder
D3: D; D_0805_2012Metric_Pad1.15x1.40mm_HandSolder
FREQ1: LTC6906IS6_TRPBF; SOT95P280X100-6N; MPN LTC6906IS6#PBF
H1, H2, H3, H4: MountingHole; MountingHole_2.5mm
J1: Barrel_Jack_MountingPin; BarrelJack_Horizontal
J2, J9, J11: Conn_01x02_Pin; PinSocket_1x02_P2.54mm_Vertical
J3: Conn_01x03_Pin; JST_ZH_B3B-ZR_1x03_P1.50mm_Vertical
J4: Conn_01x03_Pin; PinHeader_1x03_P2.54mm_Vertical
J5: Conn_01x01_Pin; SolderWire-0.15sqmm_1x01_D0.5mm_OD1.5mm
Q1: AO3400A; SOT-23
R1: 100k; R_0805_2012Metric_Pad1.20x1.40mm_HandSolder
R5: 70; R_0805_2012Metric_Pad1.20x1.40mm_HandSolder
R6: 50; R_0805_2012Metric_Pad1.20x1.40mm_HandSolder
U3: R-78C3.3-1.0; Converter_DCDC_RECOM_R-78E-0.5_THT
U4: R-78C12-1.0; Converter_DCDC_RECOM_R-78E-0.5_THT

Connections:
+3.3V: C4.1, D1.2 (A), FREQ1.3 (DIV), FREQ1.6 (V+), J11.1, U3.3 (OUT); also elsewhere on the board
+12V: C6.1, J2.1, J3.1, R6.1, U4.3 (OUT)
+15V: C3.1, C5.1, J1.1, U3.1 (IN), U4.1 (IN)
EOSC: C1.1, FREQ1.1 (OUT), J9.1; also elsewhere on the board
GND: C1.2, C3.2, C4.2, C5.2, C6.2, FREQ1.2 (GND), J1.2, J2.2, J3.2, J4.3, J9.2, J11.2, R1.1, R5.2, U3.2 (GND), U4.2 (GND); also elsewhere on the board
unnamed: D1.1 (K), D3.2 (A)
unnamed: D3.1 (K), J3.3, Q1.3 (D)
unnamed: FREQ1.4 (SET), R1.2
unnamed: J4.1, R5.1, R6.2
unnamed: J4.2, Q1.2 (S)
unnamed: J5.1, Q1.1 (G)
PCS: Bus_D1.3; also elsewhere on the board
SDI: Bus_D1.4; also elsewhere on the board
SDO: Bus_D1.2; also elsewhere on the board
sck: Bus_D1.1; also elsewhere on the board

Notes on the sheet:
VOLTAGE REGULATOR
BARREL PIN
2/10/2026
MOUNTING HOLES
Pneumatic bottom board
1.0
PIN CONFIGURATION
MOTOR_CONTROL
ADC
EXTERNAL CLOCK

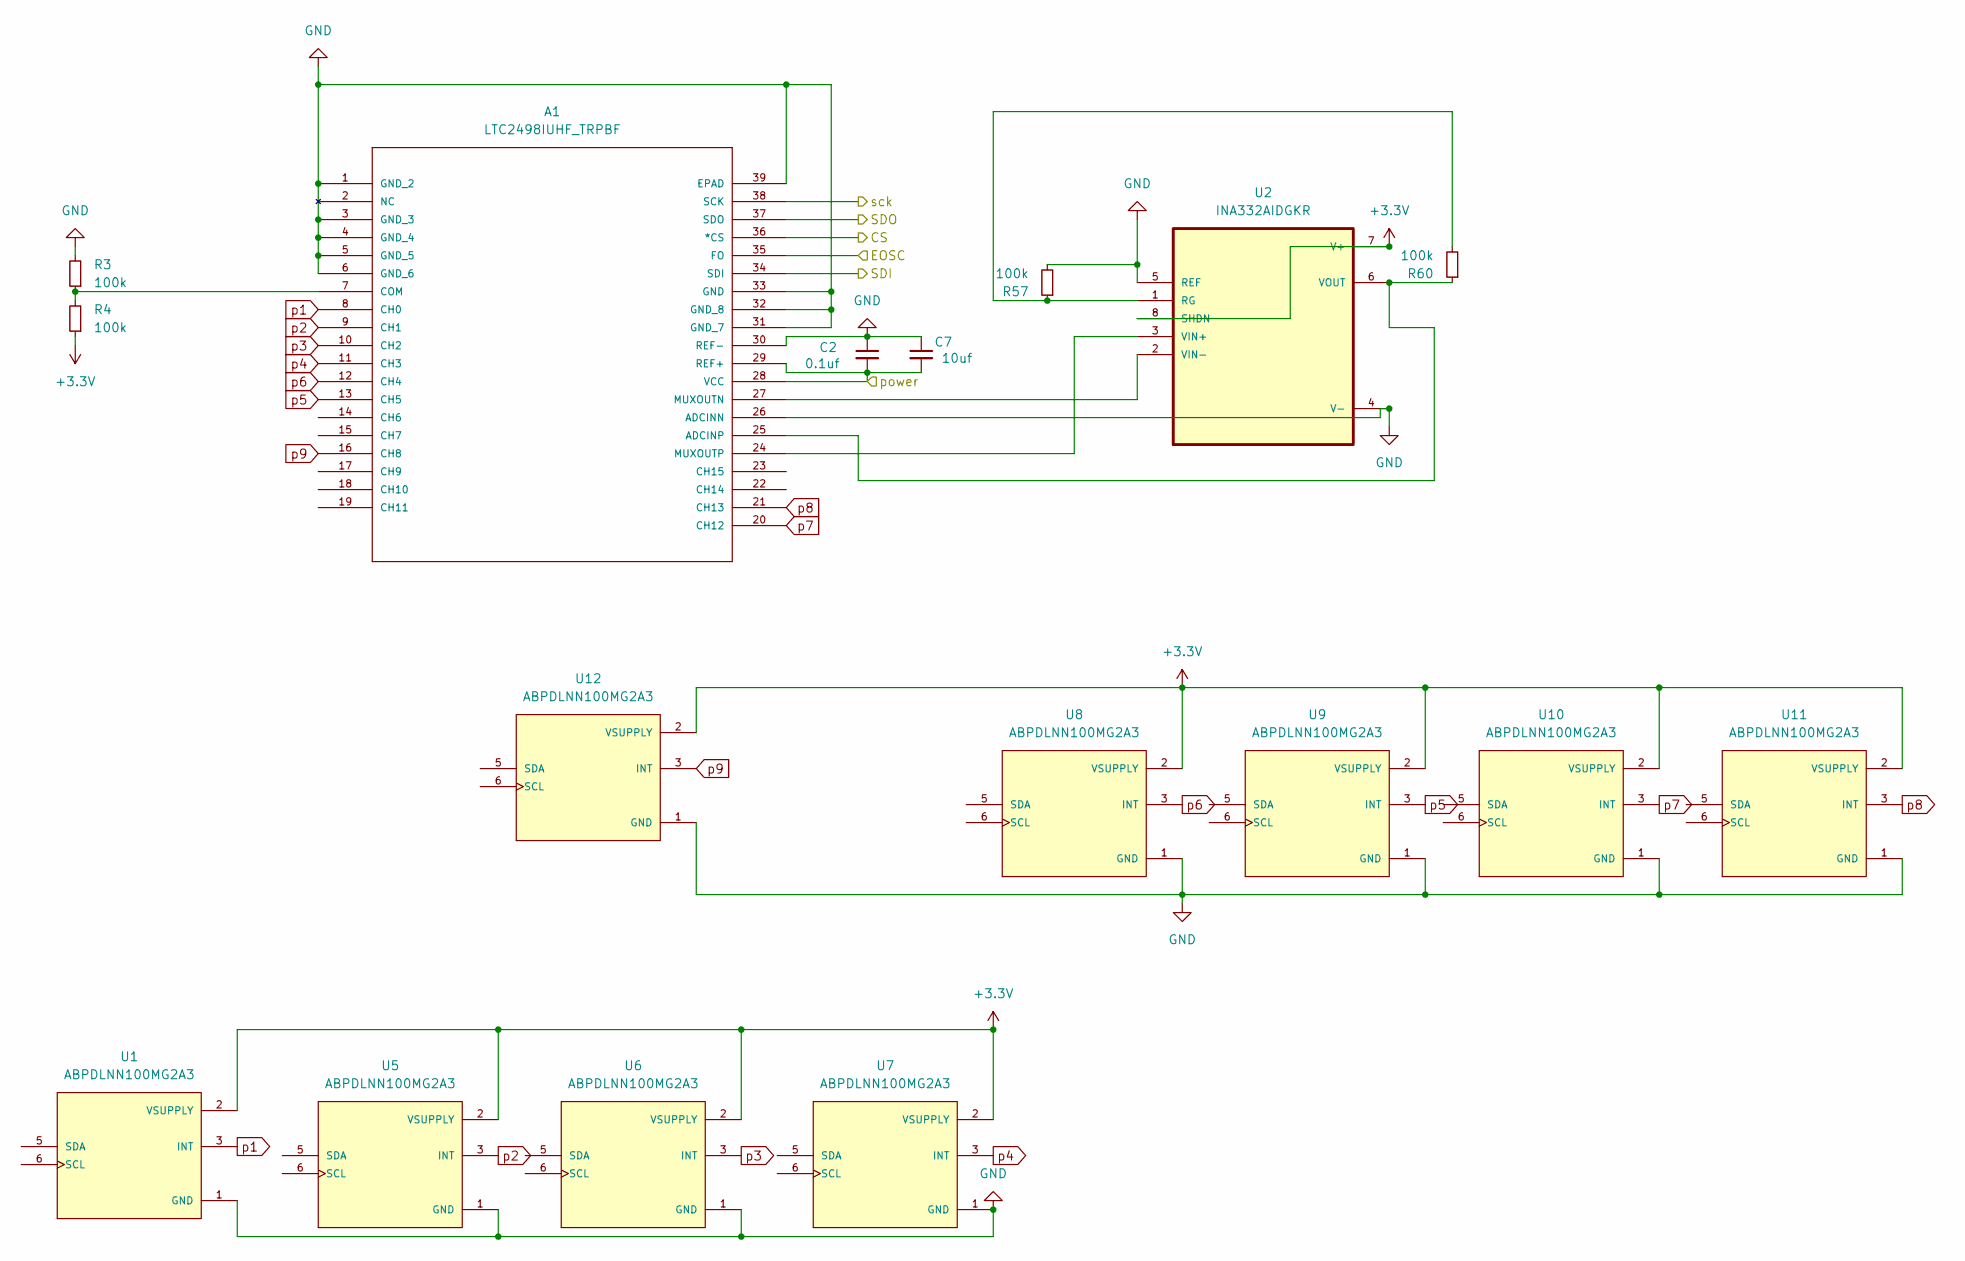
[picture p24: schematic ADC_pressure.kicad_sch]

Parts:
A1: LTC2498IUHF_TRPBF; QFN-38_UHF; MANUFACTURER_PART_NUMBER ltc2498iuhf
C2: 0.1uf; C_1206_3216Metric_Pad1.33x1.80mm_HandSolder
C7: 10uf; C_1206_3216Metric_Pad1.33x1.80mm_HandSolder
R3, R4, R57, R60: 100k; R_0805_2012Metric_Pad1.20x1.40mm_HandSolder
U1, U5, U6, U7, U8, U9, U10, U11, U12: ABPDLNN100MG2A3; XDCR_ABPDLNN100MG2A3; PARTREV E
U2: INA332AIDGKR; SOP65P490X110-8N

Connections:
+3.3V: A1.28 (VCC), A1.29 (REF+), C2.2, C7.2, R4.1, U1.2 (VSUPPLY), U2.7 (V+), U2.8 (SHDN), U5.2 (VSUPPLY), U6.2 (VSUPPLY), U7.2 (VSUPPLY), U8.2 (VSUPPLY), U9.2 (VSUPPLY), U10.2 (VSUPPLY), U11.2 (VSUPPLY), U12.2 (VSUPPLY); also elsewhere on the board
EOSC: A1.35 (FO); also elsewhere on the board
GND: A1.1 (GND_2), A1.3 (GND_3), A1.4 (GND_4), A1.5 (GND_5), A1.6 (GND_6), A1.26 (ADCINN), A1.30 (REF-), A1.31 (GND_7), A1.32 (GND_8), A1.33 (GND), A1.39 (EPAD), C2.1, C7.1, R3.2, R57.2, U1.1 (GND), U2.4 (V-), U2.5 (REF), U5.1 (GND), U6.1 (GND), U7.1 (GND), U8.1 (GND), U9.1 (GND), U10.1 (GND), U11.1 (GND), U12.1 (GND); also elsewhere on the board
unnamed: A1.25 (ADCINP), R60.1, U2.6 (VOUT)
unnamed: A1.7 (COM), R3.1, R4.2
unnamed: A1.27 (MUXOUTN), U2.2 (VIN-)
unnamed: A1.24 (MUXOUTP), U2.3 (VIN+)
unnamed: R57.1, R60.2, U2.1 (RG)
PCS: A1.36 (*CS); also elsewhere on the board
SDI: A1.34 (SDI); also elsewhere on the board
SDO: A1.37 (SDO); also elsewhere on the board
p1: A1.8 (CH0), U1.3 (INT)
p2: A1.9 (CH1), U5.3 (INT)
p3: A1.10 (CH2), U6.3 (INT)
p4: A1.11 (CH3), U7.3 (INT)
p5: A1.13 (CH5), U9.3 (INT)
p6: A1.12 (CH4), U8.3 (INT)
p7: A1.20 (CH12), U10.3 (INT)
p8: A1.21 (CH13), U11.3 (INT)
p9: A1.16 (CH8), U12.3 (INT)
sck: A1.38 (SCK); also elsewhere on the board

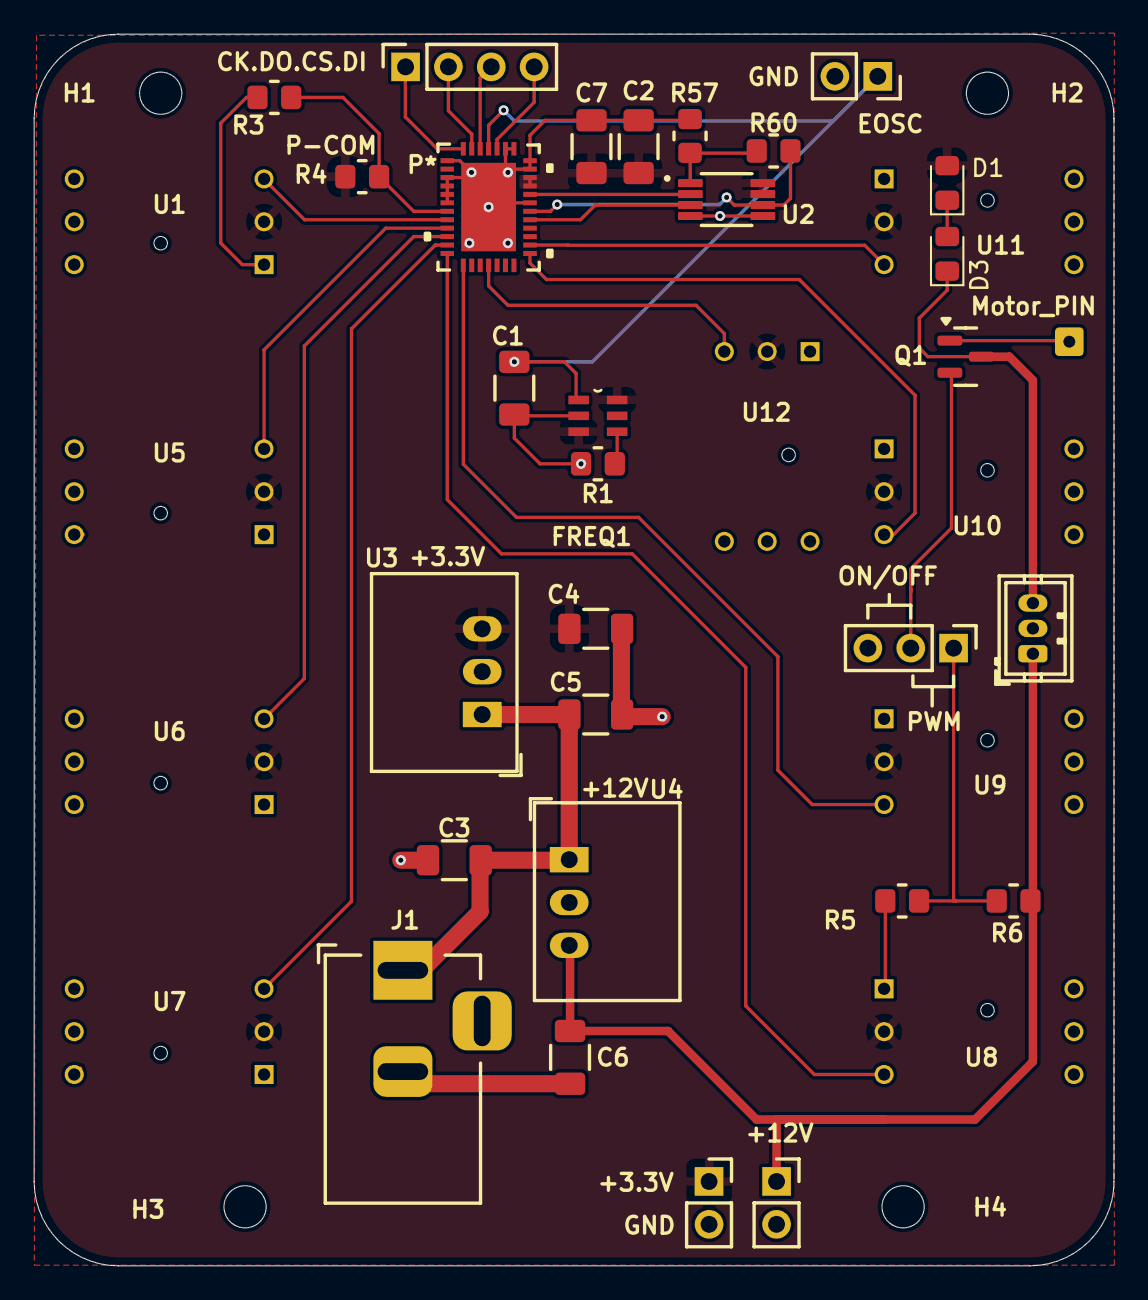
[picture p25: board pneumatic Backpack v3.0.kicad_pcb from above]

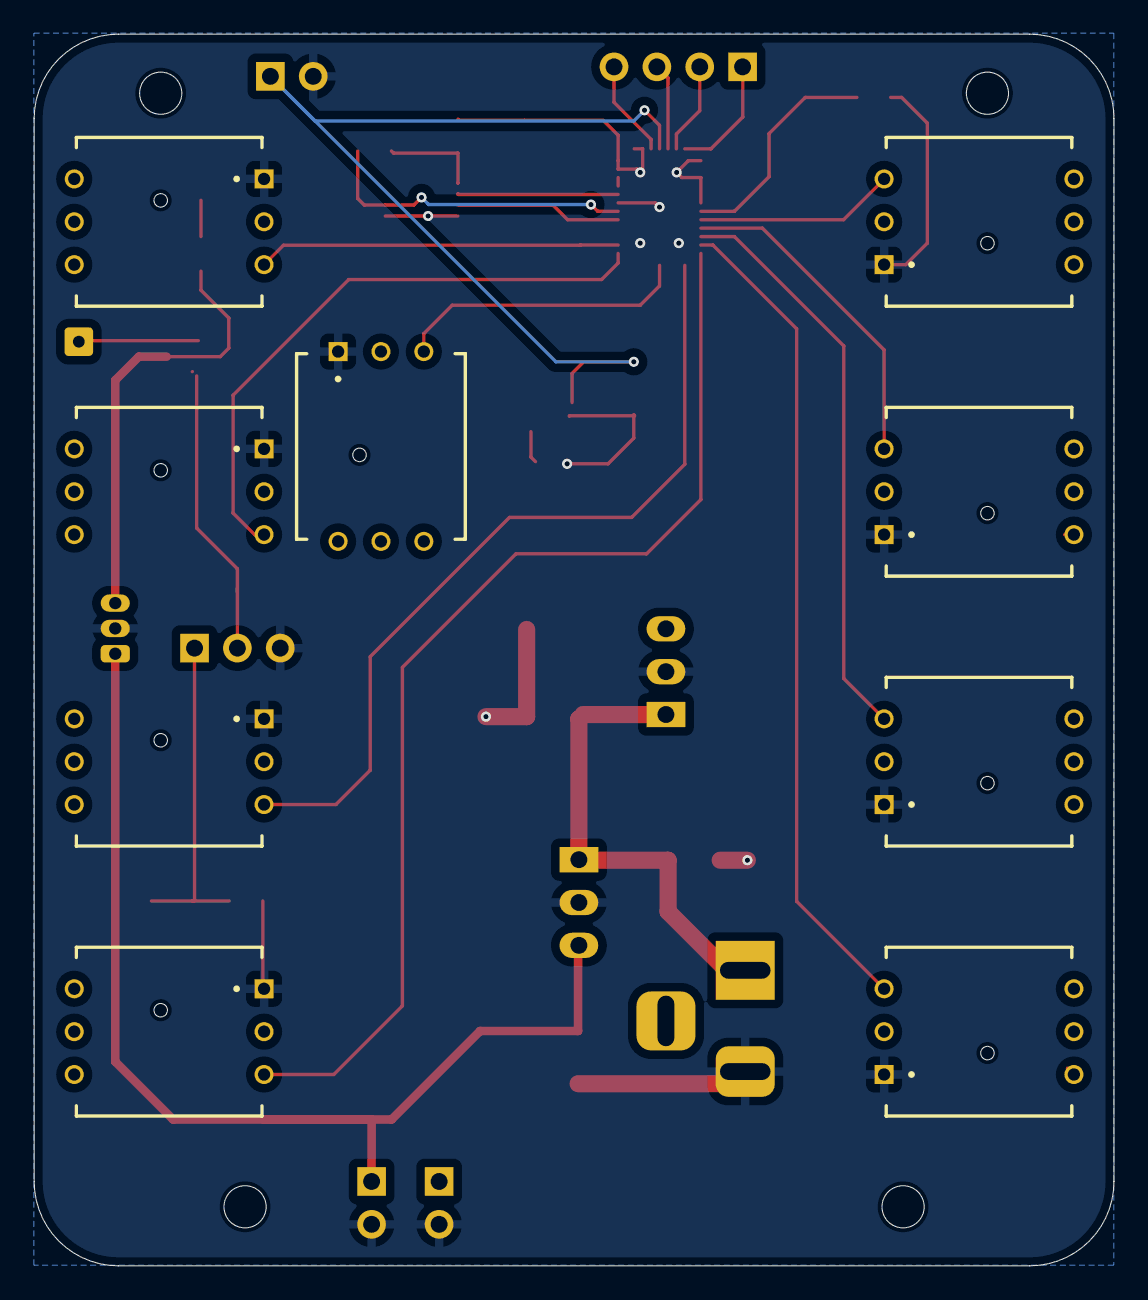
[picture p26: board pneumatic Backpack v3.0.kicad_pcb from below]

Board: 2 copper layers, 64.0 x 73.0 mm, 43 parts (9 on the bottom side), 29 nets.

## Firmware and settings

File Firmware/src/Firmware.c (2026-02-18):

#include <stdio.h>
#include "Network.h"
#include "LTC2498.h"
#include "MC33996.h"
#include "DRV8311.h"
#include "freertos/FreeRTOS.h"
#include "freertos/task.h"
#include "freertos/semphr.h"
#include "esp_log.h"
#include "Constant.h"
#include "circularBuffer.h"
#include "Rtos_tasks.h"

LTC2498 right_sensor;
LTC2498 left_sensor;
LTC2498 pressure_sensor;
MC33996 actuator;
DRV8311 motor_driver;

SemaphoreHandle_t network_sem;
SemaphoreHandle_t bus1_sem;
SemaphoreHandle_t bus2_sem;
SemaphoreHandle_t socket_mutex1;
SemaphoreHandle_t socket_mutex2;
CircularBuffer network_upload_buffer;

uint8_t differential_commands[] = {LTC2498_P0_N1,LTC2498_P2_N3,LTC2498_P4_N5,LTC2498_P6_N7,LTC2498_P8_N9,LTC2498_P10_N11,LTC2498_P12_N13,LTC2498_P14_N15};

// Initialize SPI buses
void init_spi_bus(){
    spi_bus_config_t buscfg1 = {
        .miso_io_num = MISO_PIN1,
        .mosi_io_num = MOSI_PIN1,
        .sclk_io_num = SCLK_PIN1,
        .max_transfer_sz = MAX_TRANSFER_SZ
    };
    spi_bus_config_t buscfg2 = {
        .miso_io_num = MISO_PIN2,
        .mosi_io_num = MOSI_PIN2,
        .sclk_io_num = SCLK_PIN2,
        .max_transfer_sz = MAX_TRANSFER_SZ
    };
    esp_err_t ret= spi_bus_initialize(SPI2_HOST, &buscfg1, 0);
    if (ret != ESP_OK) {
        ESP_LOGE(SPIBUS, "Failed to initialize spi bus: 1");
    }
    ret= spi_bus_initialize(SPI3_HOST, &buscfg2, 0) ;
    if (ret != ESP_OK) {
        ESP_LOGE(SPIBUS, "Failed to initialize spi bus: 2");
    }
    ESP_LOGI(SPIBUS, "SPI buses initialized");
}

// Main application
void setup(){
    init_network();
    init_spi_bus();
    init_adc(&left_sensor,SPI2_HOST,ADC_CLOCK_SPEED, ADC_MODE,ADC1_CS_PIN, QUEUE_SIZE,'l');
    init_adc(&right_sensor,SPI2_HOST,ADC_CLOCK_SPEED, ADC_MODE,ADC1_CS_PIN, QUEUE_SIZE,'r');
    init_adc(&pressure_sensor,SPI2_HOST,ADC_CLOCK_SPEED, ADC_MODE,ADC2_CS_PIN, QUEUE_SIZE,'p');
    init_MC33996(&actuator,SPI2_HOST,ADC_CLOCK_SPEED, ADC_MODE,ACTUATOR_CS_PIN, QUEUE_SIZE);
    init_drv8311(&motor_driver,SPI3_HOST,ADC_CLOCK_SPEED, ADC_MODE,MOTOR_CS_PIN, QUEUE_SIZE);
    init_circular_buffer(&network_upload_buffer, BUFFER_SIZE);
    // esp_log_level_set("*", ESP_LOG_WARN);
}

// Main function
void app_main(void){
    bus1_sem=xSemaphoreCreateMutex();
    bus2_sem=xSemaphoreCreateMutex();
    socket_mutex1=xSemaphoreCreateMutex();
    socket_mutex2=xSemaphoreCreateMutex();
    network_sem=xSemaphoreCreateBinary();
    setup();
    xSemaphoreGive(network_sem);
    xTaskCreate(set_connection, "set_connection", 2048, NULL, 5, NULL);
    xTaskCreate(read_adc, "read_right_limbs", 3072, &right_sensor, 1, NULL);
    xTaskCreate(read_adc, "read_left_limbs",3072,&left_sensor,1,NULL);
    xTaskCreate(read_adc, "read_pressure",3072, &pressure_sensor, 1, NULL);
    xTaskCreate(network_upload, "send_data", 3072, NULL, 2, NULL);
    xTaskCreate(network_download, "receive_data", 3072, NULL, 2, NULL);
    xTaskCreate(write_actuator, "solenoid",3072, NULL, 1, NULL);
    xTaskCreate(motor_control_task, "motor_control", 3072, NULL, 3, NULL);
}

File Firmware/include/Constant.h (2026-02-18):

#include "freertos/FreeRTOS.h"
#include "freertos/semphr.h"
#include "driver/spi_master.h"
#include "esp_log.h"
#include "driver/gpio.h"
#include "esp_wifi.h"
#include "nvs_flash.h"
#include "esp_netif.h"
#include "esp_event.h"
#include "lwip/sockets.h"
#include "lwip/netdb.h"


#define MISO_PIN1 13
#define MOSI_PIN1 11
#define SCLK_PIN1 12
#define MISO_PIN2 37
#define MOSI_PIN2 35
#define SCLK_PIN2 36
#define MAX_TRANSFER_SZ 4096

#define ADC_CLOCK_SPEED 1000000
#define ADC_MODE 0
#define QUEUE_SIZE 1
#define NUM_ADCS 1
#define DATA_ACCUSATION_FREQUENCY_MS 10

#define ADC1_CS_PIN 4
#define ADC2_CS_PIN 5
#define ADC3_CS_PIN 6
#define ACTUATOR_CS_PIN 7
#define MOTOR_CS_PIN 15

#define MOTOR_STATE_ORDER (uint16_t[]){0x0021, 0x0102, 0x0120, 0x0201, 0x0220, 0x0202}

#define ESP_WIFI_SSID "mqtt_client"
#define ESP_WIFI_PASS "12345678"
#define ESP_WIFI_CHANNEL 1
#define MAX_STA_CONN 2
#define PC_IP "192.168.4.1"

#define BUFFER_SIZE 100

#define SPIBUS          "spi bus"
#define NETWORK         "network"
#define ADC             "adc"
#define LIMBS           "limbs"
#define PRESSURE        "Pressure"
#define CIRCULAR_BUFF   "circular buffer"
#define SERIF           "serif"
#define ACTUATOR        "pneumatic actuator"

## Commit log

2026-02-18 Initial clean commit - firmware + PCB source only
    [ADC_diff.kicad_sch, ADC_pressure.kicad_sch, ADC_single.kicad_sch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]
2026-02-18 bom fell
    [Combined_BOM.xlsx]
2026-03-12 cleaning code
    [ADC_diff.kicad_sch, ADC_pressure.kicad_sch, ADC_single.kicad_sch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]
2026-03-12 Add interactive schematic badge to README
    Added a badge linking to the interactive schematic.
2026-03-12 Fix capitalization in PCB image rendering step
2026-03-12 Update PCB file path in workflow configuration
2026-03-12 Update PCB file path for rendering
2026-03-12 Refactor PCB image rendering workflow
    Updated workflow to improve PCB image rendering and commit process.
2026-03-12 Modify PCB render workflow to skip CI on commit
    Updated commit message to skip CI for auto-updates.
2026-03-12 Auto-update PCB renders [skip ci]
2026-03-12 Update README to streamline image section
    Removed PCB description and combined image links.
2026-03-12 Update PCB image rendering for top and bottom boards
2026-03-12 Update PCB file path for rendering workflow
2026-03-12 Update PCB image workflow to include new board version
2026-03-12 Add JLCPCB configuration for gerbers and drill files
2026-03-12 Update config path for Gerber output in workflow
2026-03-12 Set KiCad version to 8 in pcb-image.yml
    Updated KiCad board version to 8 for both v3.0 and v3.1.
2026-03-12 added diods to the leds
    [pneumatic Backpack v3.1.kicad_pcb, pneumatic Backpack v3.1.kicad_sch]
2026-03-12 Add path filter for Hardware directory in workflow
